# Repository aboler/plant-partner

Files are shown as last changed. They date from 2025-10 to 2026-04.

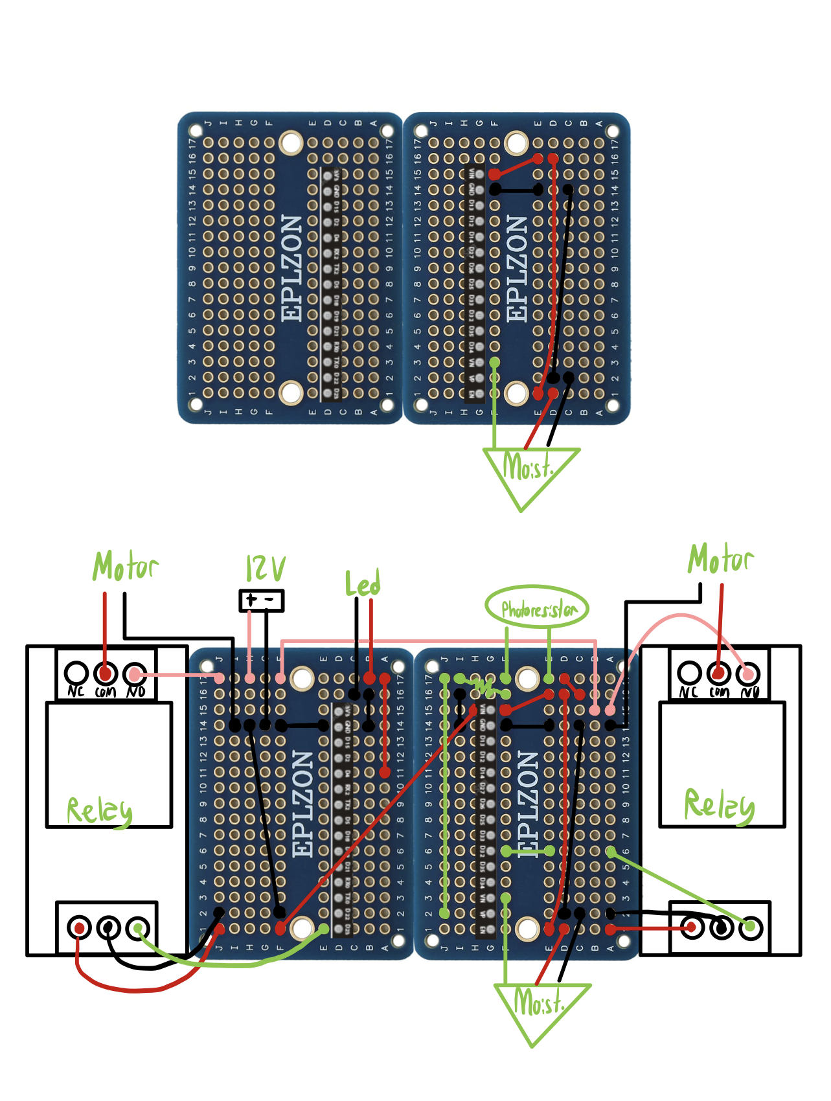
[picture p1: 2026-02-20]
Documentation/Diagrams/BetaBuild_Soldering_Moisture_TotalCircuit.png

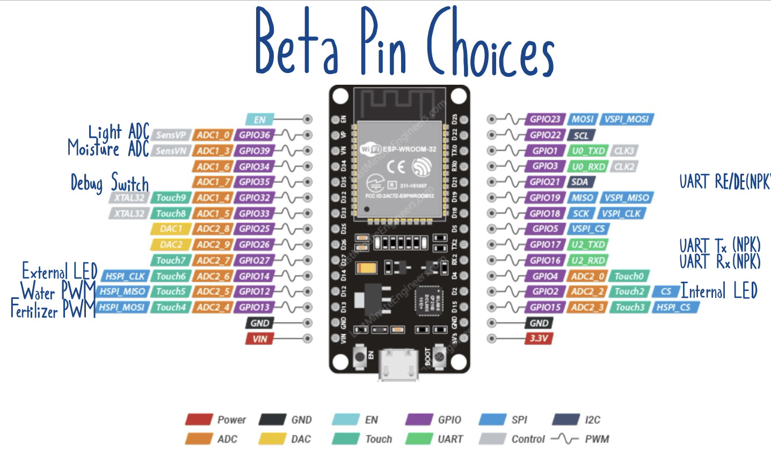
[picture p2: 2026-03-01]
Documentation/Diagrams/BetaBuild_Pinouts.png

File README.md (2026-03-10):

# plant-partner

Plant Partner repo. for CEN4908c

- **Contributors**: Nicholas Cimino, Aspen Boler, Sabrina Luu, Carter Kreis, Fernando Amado-Pupo
- [Project link](https://github.com/users/aboler/projects/1)

### Notes for adding code and time reports

- Please create a new branch to develop off of main
  - main remains as a minimum viable product branch available
  - Allows PR's to be made for adding to dev so group members can review code made
- Add reports for any changes/development work done in a day in main branch
  - Make reports in Documentation/Reports in relevant timesheet

## Meeting Times

- Meet weekly for ~15 minutes after every client meeting to ensure we're staying on track

## Completed Work

### Hardware Release

Please see ``Documentation/Diagrams``, ``Documentation/Circuits``, and ``Documentation/pcbDesign`` for current hardware designed, built, and used for testing

### Software Release

<ins>For ESP32 (in VSCode):</ins>

1. Run ``git clone recurse-submodules git@github.com:aboler/plant-partner.git``
   - This will clone the base plant-partner and esp-idf Github repositories using ssh
2. Download the ESP-IDF Extension
3. After you install the extension, the  should appear in the VS Code Activity bar (left side set of icons). When you click the Espressif icon, you can see a list of basic commands provided by this extension.
4. From the command list, select Configure ESP-IDF Extension or press F1 and type “Configure ESP-IDF Extension”. After, choose the ESP-IDF: Configure ESP-IDF Extension option.
5. Choose Express. Select Github for the download server.
6. For “Select ESP-IDF version” select “Find ESP-IDF in your system”
7. For “Enter ESP-IDF directory (IDF_PATH):” click the folder icon and within the Github Repository select /plant-partner/microSrc/submodules/esp-idf
8. For “Enter ESP-IDF Tools directory (IDF_TOOLS_PATH):” select the default location or wherever you prefer
   - Make sure that IDF_TOOLS_PATH had no spaces and is not in the Github Repo
9. If your operating system is MacOS/Linux, choose the system Python executable to create ESP-IDF virtual environment inside ESP-IDF Tools and install ESP-IDF Python package there
10. Click Install
11. If everything is installed correctly, you will see a message that all settings have been configured

In Powershell or a Linux terminal preferably:

1. Run ``cd microSrc``
2. Connect an ESP-32 into computer
3. Setup ESP-IDF and flash ESP-32 by running ``python esp.py -p PORT``
   - You may need to use python3 instead of python
   - PORT will be something like COM3 for Windows and /dev/ttyUSB0 for Ubuntu

<ins>For Backend + Database:</ins>

1. Navigate to ``backEndSrc/``
2. Start up the backend server by running ``npm start``, server will be running once these messages are displayed on the terminal
   - "Connected to MongoDB"
   - "Server running on port 8000"

<ins>For Frontend Application:</ins>

In Bash or Powershell

1. Run `cd frontEndSrc`
2. Run `cd frontend`
3. Run `flutter emulators –launch Medium_Phone_API_36.1`
4. Run `flutter pub get`
   * This command is to pull the dependencies
5. Run `flutter run`

### Pre-Alpha Build

- Ability to control GPIO Pins w/ ESP32.
  - i.e. controlling an external light source
  - Existing interfaces that allow modular control for project's purposes
- ADC data acquisition w/ ESP32
  - i.e. reading in value from photoresistor
  - Existing interfaces that allow modular control for project's purposes
- Developed basic structure to collect plant data from sensors
  - 3 uint16_t variables for collecting light, moisture, and nutrient data
- Breadboard implementation of our hardware/software
  - External photoresistor/LED circuit
- Frontend initial skeleton set up for mobile Android app interface
  - Configured Flutter environment and Android Emulator
  - Built a persistent bottom navigation bar (Tasks, Home, Settings)
  - Developed placeholder screens for each tab
  - Tested UI flow and verified emulator functionality
- Implemented locally-hosted database and backend API source code with basic functions
  - Set up MongoDB database that can be hosted locally, currently stores one JSON data model
  - Created Backend App source code with an API via Express.JS that allows for communication with the backend server and database
  - Organized the source code into folders for function controllers, JSON data models, and CRUD routes for easy addition of new functionality

### Prototype Build

- Ability to configure input GPIO Pins w/ ESP32
- Ability to generate a PWM signal
  - i.e. controlling a water pump omtor
- Modularized ADC data acquisition
  - Allows for configuration for both photoresistor and mositure sensor
- Modified breadboard implementation
  - Developed switch circuit to determine when to sample connected sensors/actuate components
  - e.g. water pump control, photoresistor and moisture sensing, LED actuation
- Ability to connect ESP32 to Wi-Fi
  - Allows new plant data to be sent to the database
- Created a test plant on the database
- Connected application and database so application can receive and display plant data to the Home tab
- Created a update button that allows application to display newly updated data from the database
- Beginnings of a PCB to replace external wiring has been started and posted to the repository
- Migrate database to the cloud via MongoDB atlas to allow for easier testing

### Alpha Build

- General clean up/organization in the code
- Modified ADC to be initialized through one function
- Modified main microcontroller loop to activate from one signal (currently a switch)
  - Reads all sensors
  - Activates actuators if needed
  - Sends data to database over Wi-Fi
- Created more permanent physical set up
  - Liquid tanks
  - Motor pumps in liquid tanks with elongated wires
  - Central cup to act as a pot
  - External carrying mechanism to more easily keep everything together
  - Smaller external circuit board
  - DAD program to act as switch, external LED, and proof that fertilizer motor activates when needed

### Beta Build

- Integrated MQTT messages to be sent from database/app. to initiate microcontroller main loop
  - ```plant_partner/act_tog_en```: toggle autocare enable
  - "plant_partner/ack"
    - w/ ```water``` msg.: actuate water pump, read moisture sensor, then report back data to the app.
    - w/ ```light``` msg.: toggle external LED, read photoresistor, then report back data to the app.
    - w/ ```nutrients``` msg.: actuate fertilizer pump
    - no message: read all of the sensors then report the data to the app.
      - If autocare enabled, then also actuate sensors based on if data requires it
- Finished and ordered PCB
- Soldered temporary physical board
- Instantiated and connected rough physical set up assembled in alpha build
- Added additional user features in the application:
  - Ability to toggle autocare and sync it with the microcontroller
  - button for actuating specific actuators
- Developed MQTT message functionality in the database
  - Time-based sample commands
  - Ability for specific actuation 

## Project Architecture

The ESP32 board is set up to interface with sensors to collect real-time environmental and system data. Currently, the microcontroller waits until it receives particular messages through an MQTT client. Depending on the message it can do the following: 1) toggle if autocare is enabled or disabled, 2) samples sensors, communicate data to the app., and actuate (if autocare on), 3) actuate a specific actuator (i.e. LED, water pump, fertilizer pump). These messages are currently being sent from the application while the sensor data is being communicated to the database.

The sensor readings can be reported to the database and displayed on a mobile application, providing users with remote monitoring. To update the data shown on the application, users must press the update button available in the Home tab. Additionally, there's a scheduling tab available where the autocare feature can be toggled as well as three actuator specific buttons for directly affecting specific devices.

### File Structure Summary

- ``microsrc`` : directory containing relevant ESP32 code
  - ``scripts`` : directory containing scripts necessary for setting up ESP-IDF dependencies and environment for device
  - ``src`` : directory containing all developed code for the program and a CMakeLists.txt to help compile
    - ``main`` : contains main program for ESP32 and CMakeLists.txt compiling developed code
    - ``dataTypes`` : contains code defining common data types created for the project, like plantData
    - ``peripherals`` : code for modularizing intercations with certain peripheral systems, like ADC, GPIO, and PWM
    - ``wifi`` : code for implementing wifi communication in the esp32
  - ``submodules`` : directory containing other repositories utilized within the main code
    - ``esp-idf`` : submodule containing examples and ESP32 interfaces in c
  - ``esp.py`` : Python script which can setup, build, flash, and/or monitor ESP-32
- ``backEndSrc`` : directory containing relevant backend code

  - ``controller`` : directory containing code for controllers that implement backend API CRUD functions for the server
    - ``sensorController.js`` : code for implementing CRUD functions that work with JSON data of the Sensor model
  - ``model`` : directory containing code for JSON data models to be used by the backend server and MongoDB database
    - ``sensorModel.js`` : code for creating the JSON Sensor data model
  - ``routes`` : directory containing code for the API's routes that allow CRUD functions to be accessed via URI in an HTTP request
    - ``sensorRoute.js`` : code for the routes that make use of functions that work with the Sensor JSON data model
  - ``node_modules`` : directory containing the node.js dependencies needed to create the backend code
  - ``.env`` : file that holds environment variables to be used by the main code of the backend server, app.js
  - ``app.js`` : the main code of the backend server, connecting to the mongoDB database, linking the routes, and locally hosting server
  - ``package-lock.json`` : the package-lock file for all the node package dependencies needed for the backend server
  - ``package.json`` : the package file listing the basic details and dependencies of the backend server project
- ``frontEndSrc`` : directory containing all Flutter/Dart source code for the mobile application.

  - ``lib``: root directory for all application logic, user interface screens, and services.
    - ``main``: application entry point; initializes the app and launches the bottom navigation shell
    - `nav.dart/dashboard_nav.dart`: bottom navigation bar widget and screen routing logic
    - ``views/``: directory containing all primary UI pages
      - `homeView.dart`: displays live plant sensor data from MongoDB and includes refresh functionality.
      - `taskView.dart/settingsView.dart:` placeholder screen for task/scheduling and user settings
      - `addPlantView.dart`: screen for adding new plants (prototype stage)
    - `services/`: directory for backend communication modules
      - `remote_service.dart`: handles HTTP requests to the backend
    - `plant.dart`: types data model used to decode JSON plant objects from the database

- ``Documentation`` : directory containing relevant project documentation
  - ``Circuits`` : directory containing relevant circuits created during development
  - ``ClassSubmissions`` : directory containing a file with the link to the Google Drive folder containing all of our report work/submissions
  - ``Contributions`` : directory containing all members' timesheet records
  - ``Datasheets`` : directory containing schematics to reference for our current materials being used
  - ``Diagrams`` : directory containing relevant diagrams created during development
  - ``Materials`` : directory containing documentation related to materials, such as which items were purchased and from where
  - ``Mosquitto`` : directory containing configuration files needed to successfully run mosquitto with our program
  - ``Research`` : directory containing research collected during the project, such as how to set up a coding environment for the ESP32
  - ``pcbDesign`` : directory containing work dones towards designing/building our project's PCB

## How to Use esp.py

PORT: This is USB port that the ESP-32 is connected to. For Windows, it should be COM3 or something similar. For Ubuntu, it should be ``/dev/ttyUSB0`` or something similar. Be aware, that if the Port is not automatically detected (usually Windows) you may have to install a driver being Silicon Labs CP210x or FTDI.

- Default: ``python esp.py -p PORT``
  - This will run the necessary setup scripts to install the ESP-IDF dependencies then build, flash, and monitor the ESP-32 at PORT
- Build: ``python esp.py build``
  - This will only build the current code under microSrc/src
- Flash: ``python esp.py flash -p PORT``
  - This will build and flash the current code under microSrc/src onto the ESP-32 at the connected Port
- Monitor: ``python esp.py monitor -p PORT``
  - This will monitor the ESP-32 at the connected Port and fill the terminal with any outputs from the ESP-32
- Clean: ``python esp.py clean``
  - This will delete any build artifacts

N.B. You may have to use python3 instead of python

## Current Bugs:

The system is in a development state with only base-level functionality implemented. No bugs reported

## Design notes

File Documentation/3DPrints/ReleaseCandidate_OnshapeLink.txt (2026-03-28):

Release Candidate:
https://cad.onshape.com/documents/16ddb73816ba2f326a677512/w/f05236e3a09f18a2d03a4be6/e/e1413465b117eccbdb8666b1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

Release Candidate Fix:
https://cad.onshape.com/documents/8866bfa4c7f7b88170b70fe7/w/29c6b3a1f68dc6e10564c710/e/2286aab6ed8d3c84d318de95

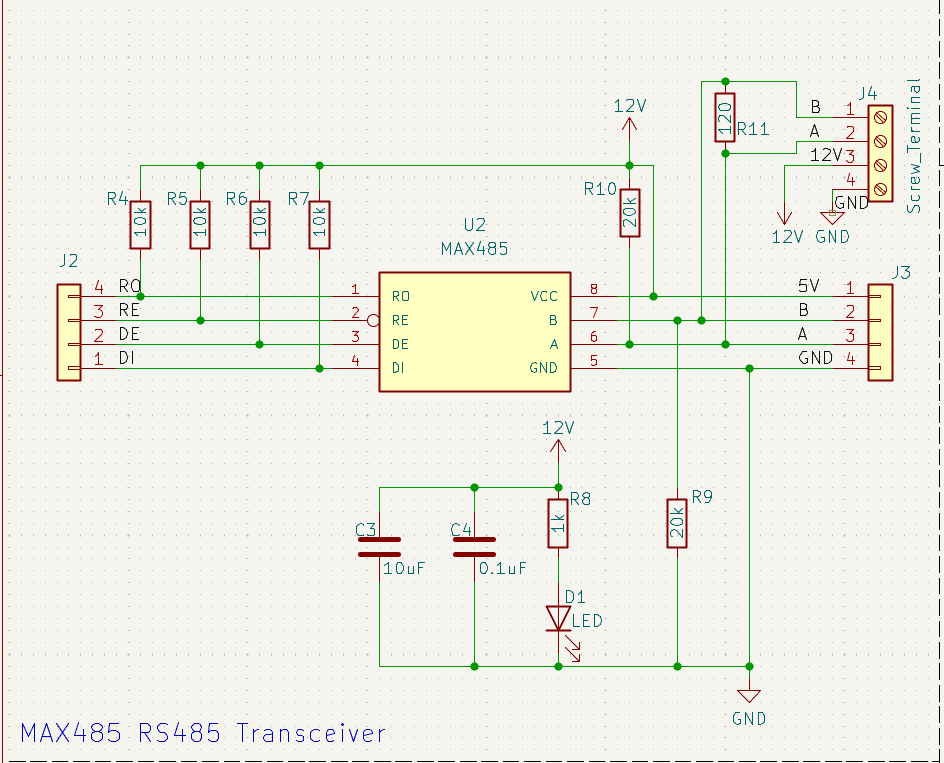
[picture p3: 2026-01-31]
Documentation/Diagrams/PCB_RS485Schematic.png

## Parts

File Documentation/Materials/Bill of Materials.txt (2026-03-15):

CEN4907C 
Plant-Partner 
Bill of Materials Draft

______________________________________
uController: ESP32Wroom: https://www.alibaba.com/product-detail/esp32-dev-kit-c-devkitc-v4_1600232911068.html
https://www.amazon.com/ESP-WROOM-32-Development-Microcontroller-Integrated-Compatible/dp/B08D5ZD528?th=1
______________________________________
Sensors:
NPK:
https://www.alibaba.com/product-detail/7-in-1-Soil-Integrated-Sensor_1601229125395.html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
Communication Protocol: Outputs RS485

Corossion Resistance Capacitive Soil Moisture Sensor:
https://www.amazon.com/Gikfun-Capacitive-Corrosion-Resistant-Detection/dp/B07H3P1NRM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
Communication Protocol: Analog to Digital (5V input voltage with output voltage of 0-3V)
Documentation links: https://www.circuitschools.com/interface-capacitive-soil-moisture-sensor-v1-2-with-arduino-lcd-and-oled/ & https://forum.arduino.cc/t/making-sense-of-moisture-sensor-readings/1382304/17
Notes: Uses JST-PH connector (the one with clasps) and a Dupont connector (the shielded one that just slides in)

Photoresistor (Ambient Light Sensor):
https://www.amazon.com/BOJACK-Photoresistance-Sensitive-Resistor-GM5539/dp/B08BKRPBVL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
Communication Protocol: Analog to Digital
Documentation links: https://www.micros.com.pl/mediaserver/info-orrgl5539.pdf 

RS485-UART Transceiver:
https://www.amazon.com/Transceiver-Featuring-Instrument-Communication-Development/dp/B00NIOLNAG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
Communication Protocol: Takes in RS485 from NPK Sensor and turns it to UART
Documentation Links: https://www.flywing-tech.com/blog/max485-ic-rs-485-communication-driver-pinout-datasheet-applications/ 

______________________________________
Pump Circuit:
* Makerverse Motor Controller: 
https://core-electronics.com.au/makerverse-motor-driver-2-channel.html
Communication Protocol: PWM 

Fluid Motor Pumps:
https://www.amazon.com/ALAMSCN-Submersible-Aquariums-Fountain-Hydroponics/dp/B08PBQ1N1G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
Thread Size: 12/24

5V Relay:
https://www.amazon.com/AEDIKO-Channel-Optocoupler-Isolation-Support/dp/B095YD3732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
Documentation: https://k6jca.blogspot.com/2022/05/schematic-amazon-relay-module-1-channel.html
 ______________________________________
Power Supply
12 V adapter:
https://www.alibaba.com/product-detail/Factory-Price-OEM-FCC-RoHS-Power_1600555965961.html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

Buck Converter down to 	5 V:
https://www.adafruit.com/product/4739
Documentation: Schematic file is in Documentation/Datasheets and the KiCad Project for it is in pcbDesign/buckConverter

LED Lamp 5V:
https://www.amazon.com/dp/B084ZNG43H?ref=ppx_yo2ov_dt_b_fed_asin_title
______________________________________
Container:
Lamp arm:
https://www.amazon.com/dp/B01HTIQD5G?ref=ppx_yo2ov_dt_b_fed_asin_title&th=1

Water/Fertilizer containers:
https://www.amazon.com/dp/B0DZNPPJRY?ref=ppx_yo2ov_dt_b_fed_asin_title

Resources:
Sensors:
NPK: https://www.instructables.com/Arduino-Soil-NPK-Sensor-Maximizing-Plant-Nutrition/
Pump:
https://core-electronics.com.au/guides/arduino/how-to-control-a-pump-with-an-arduino/

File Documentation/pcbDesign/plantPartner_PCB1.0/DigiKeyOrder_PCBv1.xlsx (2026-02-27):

# | QUANTITY | PART NUMBER | MANUFACTURER PART NUMBER | DESCRIPTION | CUSTOMER REFERENCE | BACKORDER | UNIT PRICE | EXTENDED PRICE
1 | 12 | 2057-PH2-08-UA-ND | PH2-08-UA | CONN HEADER VERT 8POS 2.54MM |  | 0 | 0.128 | 1.54
2 | 10 | 732-5327-ND | 61301611121 | CONN HEADER VERT 16POS 2.54MM |  | 0 | 0.752 | 7.52
3 | 10 | 1080-1037-ND | EL357N-G | OPTOISO 3.75KV 1CH TRANS 4-SOP |  | 0 | 0.394 | 3.94
4 | 4 | CP-002A-ND | PJ-002A | CONN PWR JACK 2X5.5MM SOLDER |  | 0 | 0.47 | 1.88
5 | 6 | ED10561-ND | OSTVN02A150 | TERM BLK 2P SIDE ENT 2.54MM PCB |  | 0 | 0.87 | 5.22
6 | 6 | ED10562-ND | OSTVN03A150 | TERM BLK 3P SIDE ENT 2.54MM PCB |  | 0 | 1.26 | 7.56
7 | 3 | ED10563-ND | OSTVN04A150 | TERM BLK 4P SIDE ENT 2.54MM PCB |  | 0 | 1.63 | 4.89

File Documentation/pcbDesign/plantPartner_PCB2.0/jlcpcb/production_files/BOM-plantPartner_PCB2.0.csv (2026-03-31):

Comment | Designator | Footprint | LCSC | Quantity
0.1uF | C7,C8 | C_0603_1608Metric | C14663 | 2
0.1uF | C4 | C_0402_1005Metric | C1525 | 1
100 | R13,R15,R25 | R_0402_1005Metric | C25076 | 3
100k | R1,R2 | R_0402_1005Metric | C25741 | 2
10k | R14,R16,R27,R4,R5,R6,R7 | R_0402_1005Metric | C25744 | 7
10uF | C3 | C_0402_1005Metric | C15525 | 1
120 | R11 | R_0402_1005Metric | C25079 | 1
18k | R3 | R_0603_1608Metric | C25810 | 1
1k | R12,R22,R23,R24,R8 | R_0402_1005Metric | C11702 | 5
20k | R10,R9 | R_0402_1005Metric | C25765 | 2
22uF | C1,C2 | C_0603_1608Metric | C59461 | 2
47uF | C10,C5,C6,C9 | C_0805_2012Metric | C16780 | 4
680 | R17 | R_0603_1608Metric | C23228 | 1
AO3400A | Q1,Q2,Q4 | SOT-23 | C20917 | 3
LED | D1,D10,D4 | LED_0603_1608Metric | C2286 | 3
MAX485 | U2 | SO08 | C19738 | 1
MPM3610 | IC1 | MPM3610 | C5173872 | 1
SS14 | D2,D3,D5,D6 | D_SMA | C2480 | 4
ESP32-DEVKIT-V1 | U3 | MODULE_ESP32_DEVKIT_V1 |  | 1
Screw_Terminal_01x02 | J30 | TerminalBlock_Phoenix_MPT-0,5-2-2.54_1x02_P2.54mm_Horizontal |  | 1
Conn_01x02 | J29 | PinHeader_1x02_P2.54mm_Vertical |  | 1
Conn_01x01 | J28 | PinHeader_1x01_P2.54mm_Vertical |  | 1
Conn_01x01 | J27 | PinHeader_1x01_P2.54mm_Vertical |  | 1
Conn_01x01 | J26 | PinHeader_1x01_P2.54mm_Vertical |  | 1
Conn_01x01 | J25 | PinHeader_1x01_P2.54mm_Vertical |  | 1
Conn_01x01 | J23 | PinHeader_1x01_P2.54mm_Vertical |  | 1
Conn_01x04 | J22 | PinHeader_1x04_P2.54mm_Vertical |  | 1
Conn_01x05 | J21 | PinHeader_1x05_P2.54mm_Vertical |  | 1
Conn_01x04 | J20 | PinHeader_1x04_P2.54mm_Vertical |  | 1
Conn_01x03 | J17 | PinHeader_1x03_P2.54mm_Vertical |  | 1
Conn_01x01 | J16 | PinHeader_1x01_P2.54mm_Vertical |  | 1
Conn_01x02 | J11 | PinHeader_1x02_P2.54mm_Vertical |  | 1
Screw_Terminal_01x02 | J10 | TerminalBlock_Phoenix_MPT-0,5-2-2.54_1x02_P2.54mm_Horizontal |  | 1
Screw_Terminal_01x02 | J9 | TerminalBlock_Phoenix_MPT-0,5-2-2.54_1x02_P2.54mm_Horizontal |  | 1
Conn_01x01 | J8 | PinHeader_1x01_P2.54mm_Vertical |  | 1
Screw_Terminal_01x02 | J7 | TerminalBlock_Phoenix_MPT-0,5-2-2.54_1x02_P2.54mm_Horizontal |  | 1
Barrel_Jack | J6 | BarrelJack_GCT_DCJ200-10-A_Horizontal |  | 1
Conn_01x02 | J5 | PinHeader_1x02_P2.54mm_Vertical |  | 1
Screw_Terminal_01x04 | J4 | TerminalBlock_Phoenix_MPT-0,5-4-2.54_1x04_P2.54mm_Horizontal |  | 1
Conn_01x04 | J3 | PinHeader_1x04_P2.54mm_Vertical |  | 1
Conn_01x04 | J2 | PinHeader_1x04_P2.54mm_Vertical |  | 1
Conn_01x04 | J1 | PinHeader_1x04_P2.54mm_Vertical |  | 1
Conn_01x03 | J13 | PinHeader_1x03_P2.54mm_Vertical |  | 1
Conn_01x03 | J12 | PinHeader_1x03_P2.54mm_Vertical |  | 1
Conn_01x03 | J14 | PinHeader_1x03_P2.54mm_Vertical |  | 1
Conn_01x03 | J18 | PinHeader_1x03_P2.54mm_Vertical |  | 1
Conn_01x03 | J15 | PinHeader_1x03_P2.54mm_Vertical |  | 1
Conn_01x04 | J19 | PinHeader_1x04_P2.54mm_Vertical |  | 1

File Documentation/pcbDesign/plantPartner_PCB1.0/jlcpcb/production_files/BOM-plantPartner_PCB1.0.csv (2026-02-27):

Comment | Designator | Footprint | LCSC | Quantity
0.1uF | C4 | C_0402_1005Metric | C1525 | 1
100 | R25 | R_0402_1005Metric | C25076 | 1
100k | R1,R2 | R_0402_1005Metric | C25741 | 2
10k | R14,R19,R27,R4,R5,R6,R7 | R_0402_1005Metric | C25744 | 7
10uF | C3 | C_0402_1005Metric | C15525 | 1
120 | R11 | R_0402_1005Metric | C25079 | 1
1N4148W | D4,D7 | D_SOD-123 | C2128 | 2
1k | R12,R16,R17,R21,R22,R23,R24,R26,R8 | R_0402_1005Metric | C11702 | 9
20k | R10,R9 | R_0402_1005Metric | C25765 | 2
22uF | C1,C2 | C_0603_1608Metric | C59461 | 2
470 | R15,R20 | R_0402_1005Metric | C25117 | 2
AO3400A | Q4 | SOT-23 | C20917 | 1
LED | D1,D10,D11,D2,D3,D5,D6 | LED_0603_1608Metric | C2286 | 7
PNP | Q1,Q2 | TO-92 | C8326 | 2
SS14 | D8,D9 | D_SMA | C2480 | 2
Conn_02x04_Top_Bottom | J20 | PinHeader_2x04_P2.54mm_Vertical |  | 1
500 | R13 | R_0603_1608Metric |  | 1
Screw_Terminal_01x02 | J30 | TerminalBlock_Phoenix_MPT-0,5-2-2.54_1x02_P2.54mm_Horizontal |  | 1
Conn_01x04 | J1 | PinHeader_1x04_P2.54mm_Vertical |  | 1
Screw_Terminal | J4 | TerminalBlock_Phoenix_MPT-0,5-4-2.54_1x04_P2.54mm_Horizontal |  | 1
Conn_01x04 | J16 | PinHeader_1x04_P2.54mm_Vertical |  | 1
Conn_01x02 | J11 | PinHeader_1x02_P2.54mm_Vertical |  | 1
Conn_02x04_Top_Bottom | J8 | PinHeader_2x04_P2.54mm_Vertical |  | 1
Conn_01x01 | J27 | PinHeader_1x01_P2.54mm_Vertical |  | 1
Conn_01x04 | J22 | PinHeader_1x04_P2.54mm_Vertical |  | 1
Conn_01x02 | J29 | PinHeader_1x02_P2.54mm_Vertical |  | 1
MAX485 | U2 | SO08 |  | 1
Conn_01x04 | J3 | PinHeader_1x04_P2.54mm_Vertical |  | 1
Conn_01x01 | J26 | PinHeader_1x01_P2.54mm_Vertical |  | 1
SRD-05VDC-SL-C | K2 | RELAY_SRD-05VDC-SL-C |  | 1
Conn_01x04 | J2 | PinHeader_1x04_P2.54mm_Vertical |  | 1
Conn_01x02 | J5 | PinHeader_1x02_P2.54mm_Vertical |  | 1
Conn_01x03 | J24 | PinHeader_1x03_P2.54mm_Vertical |  | 1
EL357N-G | U4 | OPTO_EL357N-G |  | 1
Conn_01x03 | J9 | PinHeader_1x03_P2.54mm_Vertical |  | 1
18.7k | R3 | R_0603_1608Metric |  | 1
Conn_01x03 | J25 | PinHeader_1x03_P2.54mm_Vertical |  | 1
500 | R18 | R_0603_1608Metric |  | 1
Conn_01x03 | J14 | PinHeader_1x03_P2.54mm_Vertical |  | 1
Conn_01x03 | J12 | PinHeader_1x03_P2.54mm_Vertical |  | 1
Conn_01x03 | J17 | PinHeader_1x03_P2.54mm_Vertical |  | 1
Conn_01x04 | J21 | PinHeader_1x04_P2.54mm_Vertical |  | 1
Screw_Terminal_01x03 | J6 | TerminalBlock_Phoenix_MPT-0,5-3-2.54_1x03_P2.54mm_Horizontal |  | 1
Conn_01x03 | J7 | PinHeader_1x03_P2.54mm_Vertical |  | 1
MPM3610 | IC1 | MPM3610 |  | 1
Screw_Terminal_01x02 | J18 | TerminalBlock_Phoenix_MPT-0,5-2-2.54_1x02_P2.54mm_Horizontal |  | 1
Conn_01x01 | J28 | PinHeader_1x01_P2.54mm_Vertical |  | 1
ESP32-DEVKIT-V1 | U3 | MODULE_ESP32_DEVKIT_V1 |  | 1
SRD-05VDC-SL-C | K1 | RELAY_SRD-05VDC-SL-C |  | 1
Conn_01x03 | J15 | PinHeader_1x03_P2.54mm_Vertical |  | 1
Conn_01x03 | J13 | PinHeader_1x03_P2.54mm_Vertical |  | 1
Conn_01x01 | J23 | PinHeader_1x01_P2.54mm_Vertical |  | 1
Screw_Terminal_01x03 | J10 | TerminalBlock_Phoenix_MPT-0,5-3-2.54_1x03_P2.54mm_Horizontal |  | 1
Barrel_Jack | J19 | BarrelJack_GCT_DCJ200-10-A_Horizontal |  | 1
EL357N-G | U1 | OPTO_EL357N-G |  | 1

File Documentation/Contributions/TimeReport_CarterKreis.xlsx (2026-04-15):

Name: | Carter Kreis |  | Total Time: | 155:03:00
Date: | General Category: | Starting Time: | Ending Time: | Calculated Time Worked: | Description:
2025-10-03 | Design Draft | 11:17:00 | 14:39:00 | 3:22:00 | Sat down with group after class to define project and talk through all of Design Draft points (Deliverables, Requirements, Division of work, ect.)
2025-10-06 | Check-in | 15:00:00 | 15:32:00 | 0:32:00 | Check-in 1: Met with group & Tyler. Discussed our design draft, and asked questions regarding design plan and material buying
2025-10-12 | Project Organization | 19:17:00 | 20:00:00 | 0:43:00 | Researched and implemented Github webhook which sends all updates from Github to Discord channel named github-updates
2025-10-14 | Check-in | 11:20:00 | 11:51:00 | 0:31:00 | Check-in 2: Met with group & Tyler. Reviewed out submitted design draft, discussed adding more hardware specification, and discussed with group members to start buying materials and beginning research
2025-10-20 | Check-in | 15:00:00 | 15:32:00 | 0:32:00 | Check-in 3: Met with group & Tyler. Planned out pre-alpha build documentation, materials list, and basic codebase structure. I will be working on PCB Design and physical materials for prototypes
2025-10-20 | Pre-Alpha Build | 21:45:00 | 22:15:00 | 0:30:00 | Researched and begun setup of ESP-IDF through its VS Code extension
2025-10-24 | Pre-Alpha Build | 14:30:00 | 16:05:00 | 1:35:00 | Setup ESP-IDF extension in VS Code. Attempted Hello World example code but my laptop is not detecting ESP32 as a COM Port. We also continued to plan Pre-Alpha Build goal
2025-10-24 | Pre-Alpha Build | 19:15:00 | 20:58:00 | 1:43:00 | Repeated issues with recursively cloning the submodule esp-idf. Cloning into the submodule itself took 10-12 minutes and the first two times some of the directories failed to clone on time.
2025-10-25 | Pre-Alpha Build | 10:05:00 | 17:42:00 | 7:37:00 | Finally got the ESP-IDF to flash ESP32 after switching to my Ubuntu OS. Proceeded to research and write the code to turn on external GPIO LED that is wired on breadboard and on-board LED. Also helped containerize, clean-up, and comment overall code for Pre-Alpha Build
2025-11-04 | Design Prototype | 9:05:00 | 11:05:00 | 2:00:00 | Worked on trying to get the specific ESP-32 model by analyzing the ESP32 info structs. I also got ESP-IDF working on Windows which needed some drivers uninstalled then proper ones re-installed
2025-11-04 | Design Prototype | 13:45:00 | 14:35:00 | 0:50:00 | Setup KiCad for PCB Design. Throughout this week and the next, I will figure out specific footprints for out sensors and design the PCB Schematic and then PCB design
2025-11-06 | Design Prototype | 10:05:00 | 13:57:00 | 3:52:00 | Searched for and found my Infinity Stones (the schematics for each sensor for our PCB). Now that I gathered the schematics, I can start designing the PCB layout and how it will fit into our overall project and Design Prototype
2025-11-10 | Design Prototype | 13:30:00 | 15:51:00 | 2:21:00 | Finished PCB Schematic for Buck Converter and now working on RS-485 Transceiver Schematic.
2025-11-11 | Design Prototype | 10:30:00 | 13:00:00 | 2:30:00 | Worked on UART driver code which includes an init, read, and write functions for standard UART modules and also a skeleton for RS-485 Half-duplex UART communication with the same three main functions (init, read, write)
2025-11-13 | Design Prototype | 11:10:00 | 17:30:00 | 6:20:00 | Finished up UART driver to have init, read, and write functionality. I had to add a write_string and write_int function to make it more multi-purpose. Now its time to get the NPK Sensor readings from the RS-485 Transceiver (usins RS-485 UART mode doesn't seem practical now)
2025-11-14 | Design Prototype | 17:00:00 | 21:45:00 | 4:45:00 | With the UART driver finished, I moved onto adjusting those functions to fit NPK Sensor → RS485 Transceiver → ESP-32 Communication. With the help of Rob and some sketchy datasheets (our NPK Sensor did not provide one), I was able to receive data from the NPK Sensor. With the lack of a datasheet, we will have to test which registers contain what values, but we are at least receiving data from the sensor.
2025-11-15 | Design Prototype | 9:30:00 | 10:15:00 | 0:45:00 | Wrote initial code for espRun.sh script which should source, build, flash and monitor ESP-32 with one command. I will come back to finish and test this
2025-11-15 | Design Prototype | 14:15:00 | 20:30:00 | 6:15:00 | Finished up scripts to make working with esp-32 easier. I decided to have an intial setup script for each OS and then a big python script for actually running the configured setup. This should make development a lot more straightforward
2025-11-16 | Design Prototype | 17:15:00 | 19:15:00 | 2:00:00 | Finalized scripts for Windows since Windows is more sensitive. I ran into an issue where I wasn't calling export.bat where needed to setup idf.py but I added that call and now the script works with windows as well :)
2025-11-17 | Design Prototype | 13:05:00 | 15:35:00 | 2:30:00 | I finished the RS485 Transceiver Schematic. Added ESP32 Symbol to PCB Schematic and begun implementing 12V Relay circuit which is not looking fun
2026-01-02 | Alpha Build | 11:40:00 | 16:15:00 | 4:35:00 | After completing the 12V relay Schematic with a custom made Symbol and imported footprints, I realized that we are using 5V relays. So I have to spend more time recalculating for 5V relay values as the only schematic I could find was for the 12V.
2026-01-05 | Alpha Build | 12:15:00 | 13:45:00 | 1:30:00 | I figured out the values for the 5V relay Schematic. Next I’ll need to verify the values and then add our 12V AC/DC input to finish the schematic. Then comes laying out the PCB
2026-01-06 | Alpha Build | 9:45:00 | 11:30:00 | 1:45:00 | Added in the rest of my 5V relay Schematic component values since I got interrupted yesterday. I also found the footprints for main components in the circuit.
2026-01-23 | Alpha Build | 10:45:00 | 13:55:00 | 3:10:00 | Verified the Schematics for the RS-485 Transceiver and Buck Converter. I will verify the 5V Relay next add the 12V AC/DC input and then start routing the PCB itself (need to get here ASAP)
2026-01-24 | Alpha Build | 15:15:00 | 17:45:00 | 2:30:00 | Started verification on the 5V Relay and overestimated my circuit simulation knowledge. I started with KiCad which was bad then moved to Ltspice all while trying to simulate 5V Relay functionality with SPICE components
2026-01-26 | Alpha Build | 12:10:00 | 16:55:00 | 4:45:00 | Verified the 5V Relay in Ltspice. Now cross-checking that all the symbols and footprints match up. I also gathered some 3D models that I was missing for some components. Next, I will verify the optocoupler symbol and footprint (I think I found a better one) and then add pins to debug the PCB once printed.
2026-01-28 | Alpha Build | 16:25:00 | 18:35:00 | 2:10:00 | Put in the correct ESP32 (DEVKIT-V1) into Schematic. Updated the IO pin connections for ESP. Added Power supply system to SChematic. Need to update optocoupler symbol and footprint. Then routing shall commence
2026-01-29 | Alpha Build & Prof. Meeting | 10:10:00 | 13:10:00 | 3:00:00 | Added the small circuitry needed for ADC sensors, ESP-32 External LED, Overall PCB Heartbeat sensor. Fixed wiring issue with 5V Relays. Met with Prof. Alex about our Alpha Build status. I tried to add new optocoupler symbol and footprint but KiCad could not find it for some reason (rip). Now I need to add used ESP-32 pins, extra 5V and 12V pins, extra GND pins, and unused ESP32 Pins, THEN finally I can route (I hope … please lol).
2026-01-30 | Alpha Build | 22:00:00 | 23:15:00 | 1:15:00 | Added the optocoupler, additional 5V, 12V, and GND testing pins. Added footprints to any symbols that were missing them. Begun labeling unused ESP32 Pins on Schematic. Will add testing pins for used and unused ESP32 Pins next then routing (finally)
2026-02-05 | Beta Build | 10:40:00 | 13:45:00 | 3:05:00 | Finished adding Testing Pins. Starting Routing by drawing it out and organizing components in PCB. Quickly realized that I incorrectly setup 5V and 12V labels so will need to re-label those soon
2026-02-06 | Beta Build & Alpha Demo | 10:30:00 | 12:20:00 | 1:50:00 | We showed off the Alpha Build to Tyler and I worked on the PCB Routing. I am trying to resolve the Electrical Rules Checker (ERC) now while routing.
2026-02-07 | Beta Build | 16:45:00 | 19:30:00 | 2:45:00 | Routed the 5V Relays and fixed a schematic issue I made with them. Next is the Buck Converter, RS485 Transceiver, Power Supplies, and ESP32 Signals
2026-02-09 | Beta Build | 15:00:00 | 16:55:00 | 1:55:00 | Finished RS485 Transceiver, working on Buck Converter and connecting signals. Need to Fix Buck Converter IC footprint
2026-02-10 | Beta Build | 10:40:00 | 12:30:00 | 1:50:00 | Fixed Buck Converter and routed it. Connected more majority of ESP signals and some of the debugging pins. Brought the size of PCB down to about 1/2 of the original. My goal is to finish by today and optimize size in the 2nd gen
2026-02-11 | Beta Build | 16:00:00 | 19:30:00 | 3:30:00 | Finished Routing (for now). I need to add silkscreens for debugging, then copper pour and probably other stuff. My goal is so have a JLCPCB order by tomorrow. I brought the PCB down to about the size of my phone
2026-02-12 | Beta Build | 12:15:00 | 14:00:00 | 1:45:00 | Meeting with Instructor for Beta Build. Will work on cleaning up the wires and lessening the space that our Beta Build Takes. Will work on 3D printed box to hide wires
2026-02-12 | Beta Build | 19:00:00 | 21:15:00 | 2:15:00 | Finished Labeling PCB (too much) and fixed DRC errors on PCB. Time to add copper pours, drill holes, and probably more, then review it with a TA, and make the order :)
2026-02-13 | Beta Build | 11:00:00 | 13:10:00 | 2:10:00 | Meeting with Tyler and then working on fully implementing the RS485 Transceiver into the overall project. I also started on the 5V Lamp circuit for the PCB now (I hate Ltspice)
2026-02-13 | Beta Build | 19:15:00 | 20:05:00 | 0:50:00 | Finally got LTspice sim to work and confirmed that Schematic is good. Time to implement into PCB
2026-02-14 | Beta Build | 18:00:00 | 19:30:00 | 1:30:00 | Added Lamp to PCB. Added Copper Pours and Drill Holes. Now fixing rude error about cap. not getting copper pour connection properly
2026-02-15 | Beta Build | 21:50:00 | 23:20:00 | 1:30:00 | Gerber and Drill files have been generated. I will order on JLCPCB tomorrow morning ASAP and then finish up cube for Beta
2026-02-17 | Beta Build | 10:35:00 | 12:45:00 | 2:10:00 | Made some adjustments to PCB to fit JLCPCB standards. When going to order PCB realized I needed LCSC values. I spent the rest of the time trying to setup the JLCPCB tools plugin with zero success.
2026-02-19 | Beta Build | 10:40:00 | 13:45:00 | 3:05:00 | I got the plugin finally working! I had some messed up Python modules that I had to remove and then reinstall. I have also now learned that the footprints I chose for the PCB were too small and classified as extended for JLCPCB which means more $$. So now I have to change all the Resistor, Capacitor, and Diode footprints to a bigger size to not cost too much. This will then also result in me having to route these small parts again. I am tired of my lack of PCB design knowledge but I think I might be done after this.
2026-02-19 | Beta Build | 15:55:00 | 18:15:00 | 2:20:00 | Rerouted the resistors, capacitors, and LEDs. Surely I can now generate the Drill & Gerber files for printing with no issues
2026-02-20 | Beta Build | 11:45:00 | 18:20:00 | 6:35:00 | I ordered the PCB!! … there is so many changes I want to make but I also just wanted to order it but without the revisions it was more expensive but now we at least will have a board. Welp, either way I will solve the NPK (again unfortunately) next and then after that get onto PCB V2 and then 3D modeling
2026-02-26 | Release Candidate | 11:55:00 | 14:20:00 | 2:25:00 | Researched more into implemented PWM driven MOSFET circuit to replace 5V relays. Tested liquid pumps to see what voltages were actually needed to power them and learned that 12V is wayyy overkill. I also finished schematic for new MOSFET circuits and will Ltspice next
2026-02-26 | Release Candidate | 18:20:00 | 19:50:00 | 1:30:00 | I still need to test MOSFET circuits in Ltspice but I cleaned up the v2 Schematic and starting routing v2 PCB
2026-02-28 | Release Candidate | 18:20:00 | 19:30:00 | 1:10:00 | Routed v2 PCB some more. Finished routing power sources, Buck Converter, MOSFET circuits, and most of RS485 Transceiver. I forgot about Ltspice but will not next time I get a big chunk of time
2026-03-02 | Release Candidate | 10:05:00 | 12:05:00 | 2:00:00 | Meeting with Tyler. Fully finished routing MOSFET circuits, RS485 Transceiver, and some of ADC circuits. Still need to test MOSFET circuits in Ltspice, but placed most of overall PCB into a small edge cut square that is 2.5”x2.5” which is 50% smaller and cheaper.
2026-03-02 | Release Candidate | 13:45:00 | 17:00:00 | 3:15:00 | Finished routing everything. Adding silkscreens and double checking details. Next I will test in Ltspice. Hopefully, place JLC order by tonight or tomorrow
2026-03-03 | Release Candidate | 11:30:00 | 14:15:00 | 2:45:00 | Ordered PCB v2 after verifying MOSFET PWM circuits in Ltspice!! It was definitely cheaper but still just over $50 for all 5 to be assembled with SMT parts. Next I’ll work on “solving” the NPK so we can implement it to the entire system.
2026-03-04 | Release Candidate | 13:55:00 | 17:55:00 | 4:00:00 | (1st Half) I made an oopsie with PCBv2 order so I had to fix that and in the meantime I found a cheaper solution that kept the same logic of the circuits. It saved us $10 yippee. (2nd Half) I got the NPK sensor working! I adjusted the CRC checker and added a delay when switching between Receive and Transmit mode. The data looks valid and increases or decreases when in or out of dirt. Next I'll clean up the uart_rs485_read function so you can just call it and get an array of the Nutrient values in their mg/kg form. I'll also see how many delays I can remove so this won't slow down the overall setup.
2026-03-10 | Release Candidate | 11:35:00 | 13:30:00 | 1:55:00 | Finalized 3D Modeling Design with Aspen and began soldering the testing pins for PCBv1
2026-03-12 | Release Candidate | 11:00:00 | 12:45:00 | 1:45:00 | Worked on soldering PCBv1 some more. Most of the testing pins are in and all the screw terminals are in. Next will be the two SMD parts and any of the more difficult parts.
2026-03-24 | Release Candidate | 12:35:00 | 15:30:00 | 2:55:00 | Worked on Documentation over break so that’s why the long gap, but today I helped finalize the 3D modeling for the Liquid Housing, PCB Housing, and PCB Lid by adding connector pins. I also spent some time helping Nico test the entire projects connectivity but we had issues connected to WiFi for HTTP communication.
2026-03-26 | Release Candidate | 12:15:00 | 14:30:00 | 2:15:00 | Added the connection holes for the Moisture Sensor and NPK but I can get part of the Moisture Sensor sketch to be fully defined
2026-03-27 | Release Candidate | 17:30:00 | 18:45:00 | 1:15:00 | Finished soldering the Final PCB from where Aspen left off. Then I powered it on and tested all the pins to verify that the power was properly being routed and not killing anything. The ESP and PCB are all powered!
2026-03-31 | Release Candidate | 11:25:00 | 16:30:00 | 5:05:00 | The PCB works!! We tested it with every sensor all at once and it worked beautifully. I helped figure out the connections for each sensor and device while also updating the pin assignments for the ESP code based on the PCB. I also added connector holes to the Lamp Handle for the 3D model
2026-04-02 | Release Candidate | 10:15:00 | 14:00:00 | 3:45:00 | Drilled holes for fertilizer and water pump tubes and power cords. Soldered wire extensions for Lamp then heat-shrinked and taped them. Attempted to desolder Light Sensor pins on PCB to swap for Female Headers but destroyed PCB pad. For Tyler Demo tomorrow, I will make some small external circuitry but I will help solder a new board by early next week.
2026-04-03 | Release Candidate | 10:15:00 | 11:35:00 | 1:20:00 | Since we burned the Light Sensor PCB Pad, I breadboarded a quick solution. Then we demo’d our project to Tyler who said everything was good.
2026-04-14 | Post-Mortem Presentation | 12:00:00 | 14:45:00 | 2:45:00 | Worked on redesigning our 3D print to not take as long which required reducing the thickness and moving some of the connection pins and holes
 |  |  |  | 0:00:00
 |  |  |  | 0:00:00
 |  |  |  | 0:00:00
 |  |  |  | 0:00:00
 |  |  |  | 0:00:00
 |  |  |  | 0:00:00
 |  |  |  | 0:00:00
 |  |  |  | 0:00:00
 |  |  |  | 0:00:00
 |  |  |  | 0:00:00
 |  |  |  | 0:00:00
 |  |  |  | 0:00:00
 |  |  |  | 0:00:00
 |  |  |  | 0:00:00
 |  |  |  | 0:00:00
 |  |  |  | 0:00:00
 |  |  |  | 0:00:00
 |  |  |  | 0:00:00
 |  |  |  | 0:00:00
 |  |  |  | 0:00:00
 |  |  |  | 0:00:00
 |  |  |  | 0:00:00
 |  |  |  | 0:00:00
 |  |  |  | 0:00:00
 |  |  |  | 0:00:00
 |  |  |  | 0:00:00
 |  |  |  | 0:00:00
 |  |  |  | 0:00:00
 |  |  |  | 0:00:00
 |  |  |  | 0:00:00
 |  |  |  | 0:00:00
 |  |  |  | 0:00:00
 |  |  |  | 0:00:00
 |  |  |  | 0:00:00
 |  |  |  | 0:00:00
 |  |  |  | 0:00:00
 |  |  |  | 0:00:00
 |  |  |  | 0:00:00
 |  |  |  | 0:00:00
 |  |  |  | 0:00:00
 |  |  |  | 0:00:00
 |  |  |  | 0:00:00
 |  |  |  | 0:00:00
 |  |  |  | 0:00:00
 |  |  |  | 0:00:00
 |  |  |  | 0:00:00
 |  |  |  | 0:00:00
 |  |  |  | 0:00:00
 |  |  |  | 0:00:00
 |  |  |  | 0:00:00
 |  |  |  | 0:00:00
 |  |  |  | 0:00:00
 |  |  |  | 0:00:00
 |  |  |  | 0:00:00
 |  |  |  | 0:00:00
 |  |  |  | 0:00:00
 |  |  |  | 0:00:00
 |  |  |  | 0:00:00
 |  |  |  | 0:00:00
 |  |  |  | 0:00:00
 |  |  |  | 0:00:00
 |  |  |  | 0:00:00
 |  |  |  | 0:00:00
 |  |  |  | 0:00:00
 |  |  |  | 0:00:00
 |  |  |  | 0:00:00
 |  |  |  | 0:00:00
 |  |  |  | 0:00:00
 |  |  |  | 0:00:00
 |  |  |  | 0:00:00
 |  |  |  | 0:00:00
 |  |  |  | 0:00:00
 |  |  |  | 0:00:00
 |  |  |  | 0:00:00
 |  |  |  | 0:00:00
 |  |  |  | 0:00:00
 |  |  |  | 0:00:00
 |  |  |  | 0:00:00
 |  |  |  | 0:00:00
 |  |  |  | 0:00:00
 |  |  |  | 0:00:00
 |  |  |  | 0:00:00
 |  |  |  | 0:00:00
 |  |  |  | 0:00:00
 |  |  |  | 0:00:00
 |  |  |  | 0:00:00
 |  |  |  | 0:00:00
 |  |  |  | 0:00:00
 |  |  |  | 0:00:00
 |  |  |  | 0:00:00
 |  |  |  | 0:00:00
 |  |  |  | 0:00:00
 |  |  |  | 0:00:00
 |  |  |  | 0:00:00
 |  |  |  | 0:00:00
 |  |  |  | 0:00:00
 |  |  |  | 0:00:00
 |  |  |  | 0:00:00
 |  |  |  | 0:00:00
 |  |  |  | 0:00:00
 |  |  |  | 0:00:00
 |  |  |  | 0:00:00
 |  |  |  | 0:00:00
 |  |  |  | 0:00:00
 |  |  |  | 0:00:00
 |  |  |  | 0:00:00
 |  |  |  | 0:00:00
 |  |  |  | 0:00:00
 |  |  |  | 0:00:00
 |  |  |  | 0:00:00
 |  |  |  | 0:00:00
 |  |  |  | 0:00:00
 |  |  |  | 0:00:00
 |  |  |  | 0:00:00
 |  |  |  | 0:00:00
 |  |  |  | 0:00:00
 |  |  |  | 0:00:00
 |  |  |  | 0:00:00
 |  |  |  | 0:00:00
 |  |  |  | 0:00:00
 |  |  |  | 0:00:00
 |  |  |  | 0:00:00
 |  |  |  | 0:00:00
 |  |  |  | 0:00:00
 |  |  |  | 0:00:00
 |  |  |  | 0:00:00
 |  |  |  | 0:00:00
 |  |  |  | 0:00:00
 |  |  |  | 0:00:00
 |  |  |  | 0:00:00
 |  |  |  | 0:00:00
 |  |  |  | 0:00:00
 |  |  |  | 0:00:00
 |  |  |  | 0:00:00
 |  |  |  | 0:00:00

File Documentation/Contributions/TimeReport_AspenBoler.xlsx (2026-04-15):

Name: | Aspen Boler |  | Total Time: | 176:14:00
Date: | General Category: | Starting Time: | Ending Time: | Calculated Time Worked: | Description:
2025-10-03 | Design Draft/Plans | 11:17:00 | 14:39:00 | 3:22:00 | Sat down with group after class to define project and talked through all of Design Draft points (Deliverables, Requirements, Division of work, ect.)
2025-10-04 | Design Draft | 10:17:00 | 11:55:00 | 1:38:00 | Researched and wrote description for the project's deliverable artifacts
2025-10-04 | Check-in | 17:05:00 | 17:35:00 | 0:30:00 | Reserved time slots for all of the group check-ins for Senior Design 1
2025-10-05 | Design Draft | 18:14:00 | 20:30:00 | 2:16:00 | Helped rework design draft to fit within word limit
2025-10-06 | Check-in | 15:00:00 | 15:32:00 | 0:32:00 | Check-in 1: Met with group & Tyler, discussed our design draft, and asked questions regarding design plan and material buying
2025-10-10 | GitHub Creation | 10:35:00 | 11:31:00 | 0:56:00 | Created repository, added members, created Project page, and created reports directory
2025-10-12 | Webhook Set-up | 20:15:00 | 20:31:00 | 0:16:00 | Helped Nicholas, according to research done by Carter Kreis, to set up and test Webhook so GitHub pushes would send to a discord channel
2025-10-14 | Check-in | 11:20:00 | 11:51:00 | 0:31:00 | Check-in 2: Met with group & Tyler, reviewed out submitted design draft, discussed adding more hardware specification, and discussed with group members to start buying materials and begin research
2025-10-17 | Timesheet | 15:00:00 | 16:00:00 | 1:00:00 | Created Timesheet template for all members
2025-10-20 | Check-in | 15:00:00 | 15:32:00 | 0:32:00 | Check-in 3: Met with group & Tyler, discussed things to prepare for alpha build completion and resources to buy
2025-10-24 | Research | 10:58:00 | 13:43:00 | 2:45:00 | Began researching ESP32-Wroom and how to develop code; Found IDF with example/interfaces and made into submodule; Used submodule to configure ESP_IDF on Vscode and examine example projects
2025-10-24 | Pre-Alpha Dev. | 14:30:00 | 21:17:00 | 6:47:00 | Flashed onto all three ESP32's, helped members install development on computers, defined structure for Sunday's end, created main skeleton, investigated examples to create hardware drivers
2025-10-25 | Pre-Alpha Dev. | 10:00:00 | 16:25:00 | 6:25:00 | Began writing report, determined how to integrate ADC into main alongside Fernando, began creating ADC peripheral interface and editted CMakeList.txt to include it after several attempts, tried to create ADC structure to center ADC initialization in one function but failed.
2025-10-25 | Pre-Alpha Dev. | 20:26:00 | 21:50:00 | 1:24:00 | Reviewed and editted cleaned up code/ReadMe, adjusted report
2025-10-26 | Pre-Alpha Dev. | 11:00:00 | 12:00:00 | 1:00:00 | Record and edit microprocessor portion of video
2025-10-26 | Pre-Alpha Dev. | 15:50:00 | 16:25:00 | 0:35:00 | Clean up readme and edit in frontend portion of video
2025-10-28 | Check-in | 11:20:00 | 11:50:00 | 0:30:00 | Check-in 4: Met with group & Tyler, discussed how we needed to begin implementing communication for the prototype. Sat down with group and designated work to reach these goals.
2025-11-04 | Check-in | 11:20:00 | 11:50:00 | 0:30:00 | Check-in 5: Met with group & Tyler, discussed work that was completed and set up group work day for following Thursday. Also discussed what work would be completed to meet goals and beginning communication and test sensors.
2025-11-06 | Prototype Dev. | 10:10:00 | 14:51:00 | 4:41:00 | Met with group to conduct work; Researched how to use 5V Micro Submersible Mini Water Pump, discovered it needed use of PWM, configured PWM in main to test it, developed PWM peripheral module to use in main, integrated it into main, added photos, created branch for another sensor
2025-11-09 | Prototype Dev. | 11:20:00 | 12:06:00 | 0:46:00 | Began researching how Capacitive Soil Moisture Sensor should interface with the microcontroller and the type of data it outputs, started deciding how to modify ADC code to generalize and be used for both photoresitor and this sensor, made modular way to declare ADC for light or moisture sensor
2025-11-09 | Prototype Dev. | 19:20:00 | 19:40:00 | 0:20:00 | Changed file name's of ADC and related dependencies to make the module more generalizable
2025-11-10 | Prototype Dev. | 15:00:00 | 15:30:00 | 0:30:00 | Check-in 6: Met with group & Tyler, updated everyone on features currently implemented and made plans for the following Tuesday for each person to complete
2025-11-11 | Prototype Dev. | 11:00:00 | 17:39:00 | 6:39:00 | Got together, started integrating ADC branch and rearranged main to work as desired for prototype, created GPIO for inputs and started investigating interrupt system, created external switch to interface with micro, looked into getting wifi created to flash onto ESP32
2025-11-13 | Prototype Dev. | 11:00:00 | 17:43:00 | 6:43:00 | Got together with group, started doing gpio integration to set up sensor set up, created prototype board, connected and tested moisture sensor, connected and tested new photoresistor, created wires for relay and power bank and tested water motor, editted main to reflect prototype behavior
2025-11-14 | Prototype Dev. | 11:45:00 | 13:30:00 | 1:45:00 | Began looking through project requirements and making adjustments to ensure issues were updated, naming conventions were followed
2025-11-14 | Prototype Dev. | 14:10:00 | 14:59:00 | 0:49:00 | Tested Fernando's Wi-Fi contributions, altered circuit, and uploaded finished circuit onto Github
2025-11-14 | Prototype Dev. | 15:00:00 | 18:14:00 | 3:14:00 | Continued documenting stuff for prototype submission, made circuit diagrams, editted some issues discussed what needed to be continued for submittables
2025-11-14 | Prototype Dev. | 21:34:00 | 22:56:00 | 1:22:00 | Modify project display, began creating report document
2025-11-15 | Prototype Dev. | 11:06:00 | 13:30:00 | 2:24:00 | Continuing report, modified readme
2025-11-15 | Prototype Dev. | 16:34:00 | 21:25:00 | 4:51:00 | Finished my portion of the report
2025-11-15 | Prototype Dev. | 21:38:00 | 22:05:00 | 0:27:00 | Modified ReadMe, modified plant structure
2025-11-16 | Prototype Dev. | 11:23:00 | 14:55:00 | 3:32:00 | Modified report and ReadMe, began working on presentation, assisted Fernando and Nicholas test the state of the Wi-Fi from an alternate computer and integrating it into main.
2025-11-16 | Prototype Dev. | 17:50:00 | 21:30:00 | 3:40:00 | Begin working on powerpoint
2026-01-08 | Alpha Build | 14:10:00 | 19:00:00 | 4:50:00 | Experimented with ADC peripheral on DAD and reworked the peripheral so it only needs to call an initialization function in main, reworked some aspects of main to avoid bad outputs/improve organization, removed extra plant data structure, created heartbeat module
2026-01-16 | Alpha Build | 16:08:00 | 17:59:00 | 1:51:00 | Changed personal directory name and it killed everything, took me an hour but it forced me to reinstall everything to get it working
2026-01-16 | Alpha Build | 17:59:00 | 19:57:00 | 1:58:00 | Started modifying main to more closely match a routine based off of received signal from database. Also made some tickets and cleaned up code to be more organized and efficient
2026-01-21 | Alpha Build | 13:05:00 | 14:06:00 | 1:01:00 | Created pin diagram showing which pins were used for what; Integrated fertilizer pump addition to PWM and main and tested it out
2026-01-23 | Check-in | 10:40:00 | 11:49:00 | 1:09:00 | Check-in 6: Met with group & Tyler, discussed what's gotten done and what needs to get done for alpha build, showed bought materials and began observing what modifications would be needed to integrate electronics into plastic build
2026-01-23 | Alpha Build | 17:30:00 | 18:31:00 | 1:01:00 | Realized I should go ahead and have main set up for potential of boolean to change depending on if auto-scheduling/care is on; Created/modified tickets in project hub.
2026-01-26 | Alpha Build | 14:00:00 | 17:03:00 | 3:03:00 | Integrated PR into main; solder and heat shrinked additional wires to extend motor wire length; Built new mini circuit to make cleaner and tested with new motors to ensure everything still worked.
2026-01-29 | Instructor Meeting | 10:55:00 | 11:35:00 | 0:40:00 | Met up with group and instructor to discuss current project state and what needs to be done for documentation; fixed wire that fell out
2026-01-29 | Alpha Build | 16:50:00 | 16:58:00 | 0:08:00 | Merged wire motor branch
2026-02-05 | Alpha Build | 10:40:00 | 14:00:00 | 3:20:00 | Met up with group to test demo. Also received another 12v to 5v adapt, so began wire stripping and attaching fertilizer motor to a new relay; Utilized double-sided tape to rework our wire structure to make it more sound/easier to use and understand
2026-02-06 | Check-in | 10:40:00 | 12:19:00 | 1:39:00 | Check-in 7: Met with group & Tyler to demo alpha build; Discussed what needed to be done and experimented with group to get MQTT client to send a signal to the microcontroller.
2026-02-10 | Beta Build | 10:40:00 | 14:00:00 | 3:20:00 | Experimented with group and successfully got MQTT client to communicate t microcontroller. Started modifying main so the main loop would be triggered from MQTT message
2026-02-10 | Beta Build | 19:41:00 | 20:47:00 | 1:06:00 | Began cleaning up MQTT branch to prepare it for more clean merge
2026-02-10 | Beta Build | 22:48:00 | 23:59:00 | 1:11:00 | Additional cleaning, fixed merge conficts, adjusted tickets. Tested to still be able to build/flash.
2026-02-11 | Beta Build | 0:00:00 | 0:21:00 | 0:21:00 | ^^ Had to split into 2 because excel hates new days.
2026-02-11 | Beta Build | 11:21:00 | 13:42:00 | 2:21:00 | Tested MQTT on my own computer to see it still works, merged into main, updated tickets, set up rest of the code needed to test NPK sensor in person
2026-02-11 | Beta Build | 18:30:00 | 19:49:00 | 1:19:00 | Tried to flash uart to see what would happen if test ran without sensor connected and realized current pin set up killed the micro.; switched pins until main worked again, now ready for test tomorrow in person
2026-02-12 | Beta Build | 10:50:00 | 12:20:00 | 1:30:00 | Began attempting to connect NPK to microcontroller to test uart
2026-02-12 | Instructor Meeting | 12:20:00 | 12:49:00 | 0:29:00 | Met up with group and instructor to discuss current project state and what needs to be done for documentation;
2026-02-13 | Beta Build | 12:49:00 | 14:24:00 | 1:35:00 | Discussed with group our plans to get everything completed before beta uild. Continued attempting to get uart to work and failed. Created new pin out diagram
2026-02-13 | Check-in | 10:40:00 | 14:30:00 | 3:50:00 | Check-in 8: Met with group & Tyler to demo current status of beta build; Still couldn't get NPK working :(
2026-02-15 | Beta Build | 20:25:00 | 21:00:00 | 0:35:00 | Implemented ability to toggle autoschedule in main depending on different topic messages
2026-02-16 | Beta Build | 11:15:00 | 12:41:00 | 1:26:00 | Started testing NPK AND IT STILL DOESN'T WORK OH MY GOD
2026-02-17 | Beta Build | 10:40:00 | 12:48:00 | 2:08:00 | Got together as a goup and began planning phsyical layout of board
2026-02-17 | Beta Build | 13:47:00 | 17:47:00 | 4:00:00 | Finishing planning out board and began soldering. Got and tested LED and photoresistor
2026-02-19 | Beta Build | 13:40:00 | 20:09:00 | 6:29:00 | Soldered everything together, tested everything, and then burnt out everything while trying to test it all
2026-02-20 | Beta Build | 11:00:00 | 17:06:00 | 6:06:00 | Figured out what actually broke and fixed board with Sabrina. Replaced falling out wires with headers
2026-03-02 | Beta Build | 10:00:00 | 12:00:00 | 2:00:00 | Check-in 9: Met with Tyler to demo beta build
2026-03-03 | Release Candidate | 11:00:00 | 12:52:00 | 1:52:00 | Help Nick merge database into main; Made it so http requests are tried until sent for at least 5 times. Updated project issues.
2026-03-10 | Release Candidate | 10:40:00 | 13:28:00 | 2:48:00 | Discussed what needed to be done and assigned tasks regarding NPK and PCB; Talked through 3D and decided on what structures to go through with; set up documentation and delegated when and who needed to complete what
2026-03-10 | Release Candidate | 16:36:00 | 17:02:00 | 0:26:00 | Started integrating fixed NPK code into main
2026-03-10 | Release Candidate | 20:02:00 | 22:06:00 | 2:04:00 | Finished integrating fixed NPK code into main
2026-03-12 | Instructor Meeting | 11:40:00 | 12:00:00 | 0:20:00 | Met up with group and instructor to demonstrate and discuss current plans for the permenant housing/hardware for the project.
2026-03-12 | Check-in | 12:00:00 | 12:20:00 | 0:20:00 | Check-in 9: Met with tyler to show integration of current database changes into main, communication error handling, NPK integration, the current arrival and soldering of the new PCB, and the plans for the 3D printed housing.
2026-03-12 | Release Candidate | 12:20:00 | 13:39:00 | 1:19:00 | Tested NPK sensor and confirmed it worked with integrated main code. Then proceeded to complete Beta Tests notes.
2026-03-13 | Release Candidate | 18:50:00 | 21:45:00 | 2:55:00 | Worked on onshape design
2026-03-14 | Release Candidate | 12:00:00 | 15:45:00 | 3:45:00 | Worked on onshape design
2026-03-24 | Release Candidate | 11:50:00 | 13:00:00 | 1:10:00 | Brought in new PCB's and components; Discussed what should be done for the 3D CAD, work left to be done, and future meetings
2026-03-25 | Release Candidate | 9:55:00 | 11:26:00 | 1:31:00 | Worked on onshape design
2026-03-25 | Release Candidate | 15:00:00 | 16:05:00 | 1:05:00 | Worked on onshape design
2026-03-26 | Release Candidate | 10:40:00 | 12:50:00 | 2:10:00 | Soldered header pins on newly arrived PCB
2026-03-28 | Release Candidate | 10:45:00 | 15:42:00 | 4:57:00 | Fixing onshape design
2026-03-31 | Release Candidate | 10:40:00 | 15:53:00 | 5:13:00 | Helped merge and fix inconsistied encountered with new handshake protocols and app., test PCB, adjusted 3D model to fit printer
2026-04-02 | Release Candidate/Instructor Meeting | 9:35:00 | 16:19:00 | 6:44:00 | Had indstructor meeting at 12; Began integrating final build for TA demo, helped drill holes in water containers, threaded pipes through, soldered new PCB
2026-04-03 | Check-in | 10:35:00 | 11:30:00 | 0:55:00 | Check-in 10: Met with Tyler to show integration of current NPK changes, app changes and the PCB
2026-04-14 | Production Release | 10:36:00 | 11:15:00 | 0:39:00 | Modify added task changes to remove bugs
2026-04-14 | Production Release | 13:00:00 | 15:23:00 | 2:23:00 | Tested and adjusted Fernando's code with app and database. Discusses what was left that needs to be completed.
 |  |  |  | 0:00:00
 |  |  |  | 0:00:00
 |  |  |  | 0:00:00
 |  |  |  | 0:00:00
 |  |  |  | 0:00:00
 |  |  |  | 0:00:00
 |  |  |  | 0:00:00
 |  |  |  | 0:00:00
 |  |  |  | 0:00:00
 |  |  |  | 0:00:00
 |  |  |  | 0:00:00
 |  |  |  | 0:00:00
 |  |  |  | 0:00:00
 |  |  |  | 0:00:00
 |  |  |  | 0:00:00
 |  |  |  | 0:00:00
 |  |  |  | 0:00:00
 |  |  |  | 0:00:00
 |  |  |  | 0:00:00
 |  |  |  | 0:00:00
 |  |  |  | 0:00:00
 |  |  |  | 0:00:00
 |  |  |  | 0:00:00
 |  |  |  | 0:00:00
 |  |  |  | 0:00:00
 |  |  |  | 0:00:00
 |  |  |  | 0:00:00
 |  |  |  | 0:00:00
 |  |  |  | 0:00:00
 |  |  |  | 0:00:00
 |  |  |  | 0:00:00
 |  |  |  | 0:00:00
 |  |  |  | 0:00:00
 |  |  |  | 0:00:00
 |  |  |  | 0:00:00
 |  |  |  | 0:00:00
 |  |  |  | 0:00:00
 |  |  |  | 0:00:00
 |  |  |  | 0:00:00
 |  |  |  | 0:00:00
 |  |  |  | 0:00:00
 |  |  |  | 0:00:00
 |  |  |  | 0:00:00
 |  |  |  | 0:00:00
 |  |  |  | 0:00:00
 |  |  |  | 0:00:00
 |  |  |  | 0:00:00
 |  |  |  | 0:00:00
 |  |  |  | 0:00:00
 |  |  |  | 0:00:00
 |  |  |  | 0:00:00
 |  |  |  | 0:00:00
 |  |  |  | 0:00:00
 |  |  |  | 0:00:00
 |  |  |  | 0:00:00
 |  |  |  | 0:00:00
 |  |  |  | 0:00:00
 |  |  |  | 0:00:00
 |  |  |  | 0:00:00
 |  |  |  | 0:00:00
 |  |  |  | 0:00:00
 |  |  |  | 0:00:00
 |  |  |  | 0:00:00
 |  |  |  | 0:00:00
 |  |  |  | 0:00:00
 |  |  |  | 0:00:00
 |  |  |  | 0:00:00
 |  |  |  | 0:00:00
 |  |  |  | 0:00:00
 |  |  |  | 0:00:00
 |  |  |  | 0:00:00
 |  |  |  | 0:00:00
 |  |  |  | 0:00:00
 |  |  |  | 0:00:00
 |  |  |  | 0:00:00
 |  |  |  | 0:00:00
 |  |  |  | 0:00:00
 |  |  |  | 0:00:00
 |  |  |  | 0:00:00
 |  |  |  | 0:00:00
 |  |  |  | 0:00:00
 |  |  |  | 0:00:00
 |  |  |  | 0:00:00
 |  |  |  | 0:00:00
 |  |  |  | 0:00:00
 |  |  |  | 0:00:00
 |  |  |  | 0:00:00
 |  |  |  | 0:00:00
 |  |  |  | 0:00:00
 |  |  |  | 0:00:00
 |  |  |  | 0:00:00
 |  |  |  | 0:00:00
 |  |  |  | 0:00:00
 |  |  |  | 0:00:00
 |  |  |  | 0:00:00
 |  |  |  | 0:00:00
 |  |  |  | 0:00:00
 |  |  |  | 0:00:00
 |  |  |  | 0:00:00
 |  |  |  | 0:00:00
 |  |  |  | 0:00:00
 |  |  |  | 0:00:00
 |  |  |  | 0:00:00
 |  |  |  | 0:00:00
 |  |  |  | 0:00:00
 |  |  |  | 0:00:00
 |  |  |  | 0:00:00
 |  |  |  | 0:00:00
 |  |  |  | 0:00:00
 |  |  |  | 0:00:00
 |  |  |  | 0:00:00
 |  |  |  | 0:00:00
 |  |  |  | 0:00:00
 |  |  |  | 0:00:00
 |  |  |  | 0:00:00
 |  |  |  | 0:00:00

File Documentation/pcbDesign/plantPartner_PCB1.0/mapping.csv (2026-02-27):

Footprint | Part Value | LCSC Part
C1,C2 | 2 | 22uF
C3 | 1 | 10uF
C4 | 1 | 0.1uF
D1,D2,D3,D5,D6,D10,D11 | 7 | LED
D4,D7 | 2 | 1N400x
D8,D9 | 2 | SS14
IC1 | 1 | MPM3610
J1,J2,J3,J16,J21,J22 | 6 | Conn_01x04
J18,J30 | 2 | Screw_Terminal_01x02
J19 | 1 | Barrel_Jack
J23,J26,J27,J28 | 4 | Conn_01x01
J4 | 1 | Screw_Terminal
J5,J11,J29 | 3 | Conn_01x02
J6,J10 | 2 | Screw_Terminal_01x03
J7,J9,J12,J13,J14,J15,J17,J24,J25 | 9 | Conn_01x03
J8,J20 | 2 | Conn_02x04_Top_Bottom
K1,K2 | 2 | SRD-05VDC-SL-C
Q1,Q2 | 2 | PNP
Q4 | 1 | AO3400A
R1,R2 | 2 | 100k
R11 | 1 | 120
R13,R18 | 2 | 500
R15,R20 | 2 | 470
R25 | 1 | 100
R3 | 1 | 18.7k
R4,R5,R6,R7,R14,R19,R27 | 7 | 10k
R8,R12,R16,R17,R21,R22,R23,R24,R26 | 9 | 1k
R9,R10 | 2 | 20k
U1,U4 | 2 | EL357N-G
U2 | 1 | MAX485
U3 | 1 | ESP32-DEVKIT-V1

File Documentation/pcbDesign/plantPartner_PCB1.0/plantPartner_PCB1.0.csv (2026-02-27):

Reference | Qty | Value | DNP | Exclude from BOM | Exclude from Board | Footprint | Datasheet
C1,C2 | 2 | 22uF |  |  |  | Capacitor_SMD:C_0201_0603Metric | ~
C3 | 1 | 10uF |  |  |  | Capacitor_SMD:C_0201_0603Metric | ~
C4 | 1 | 0.1uF |  |  |  | Capacitor_SMD:C_0201_0603Metric | ~
D1,D2,D3,D5,D6,D10,D11 | 7 | LED |  |  |  | LED_SMD:LED_0201_0603Metric | ~
D4,D7 | 2 | 1N400x |  |  |  | Diode_THT:D_A-405_P7.62mm_Horizontal | ~
D8,D9 | 2 | SS14 |  |  |  | Diode_SMD:D_SMA | ~
IC1 | 1 | MPM3610 |  |  |  | MPM3610:MPM3610
J1,J2,J3,J16,J21,J22 | 6 | Conn_01x04 |  |  |  | Connector_PinHeader_2.54mm:PinHeader_1x04_P2.54mm_Vertical | ~
J4 | 1 | Screw_Terminal |  |  |  | TerminalBlock_Phoenix:TerminalBlock_Phoenix_MKDS-1,5-4-5.08_1x04_P5.08mm_Horizontal | ~
J5,J11,J29 | 3 | Conn_01x02 |  |  |  | Connector_PinHeader_2.54mm:PinHeader_1x02_P2.54mm_Vertical | ~
J6,J10 | 2 | Screw_Terminal_01x03 |  |  |  | TerminalBlock_Phoenix:TerminalBlock_Phoenix_MKDS-1,5-3-5.08_1x03_P5.08mm_Horizontal | ~
J7,J9,J12,J13,J14,J15,J17,J24,J25 | 9 | Conn_01x03 |  |  |  | Connector_PinHeader_2.54mm:PinHeader_1x03_P2.54mm_Vertical | ~
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

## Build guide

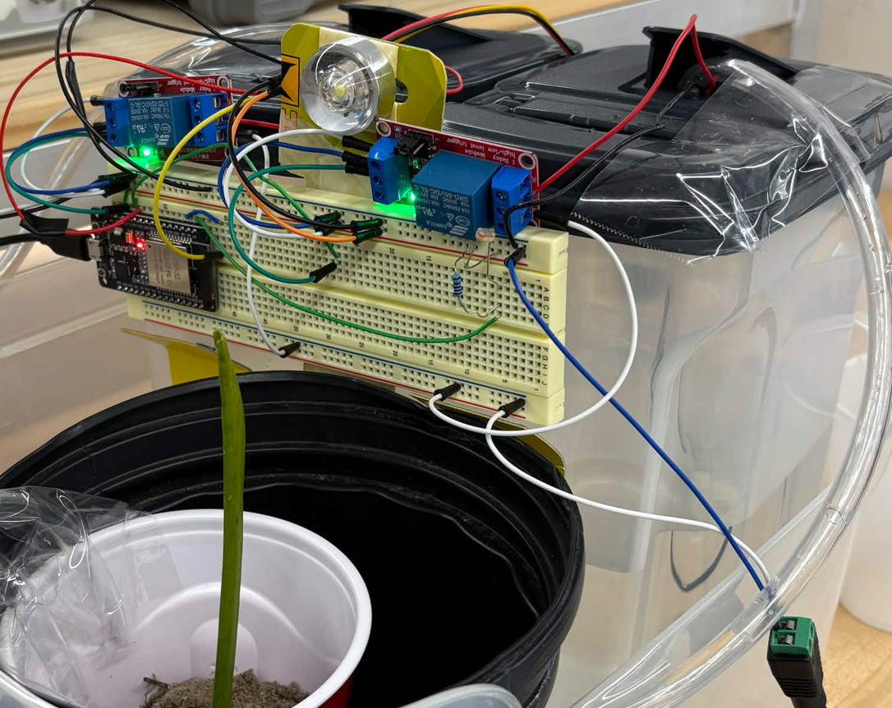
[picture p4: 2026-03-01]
Documentation/Circuits/BetaBuild_NewBreadboard.png

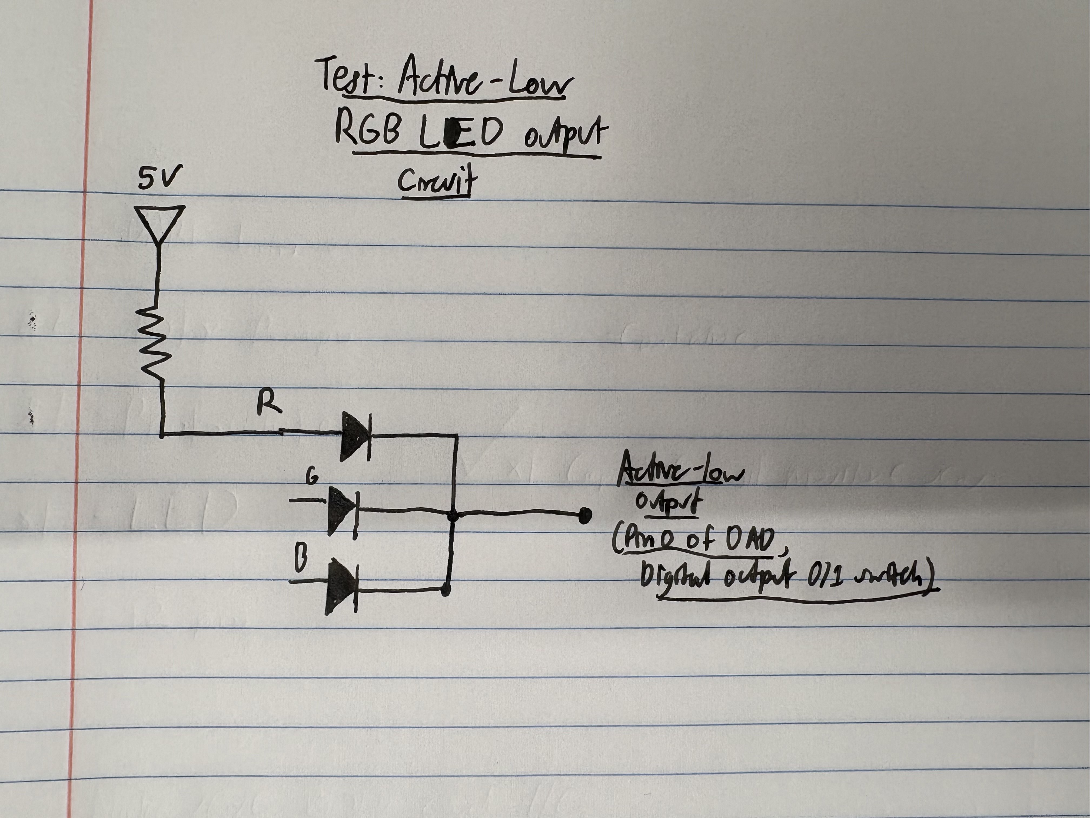
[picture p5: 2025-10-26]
Documentation/Diagrams/PreAlphaBuild_Circuit_ExternalLED.jpg

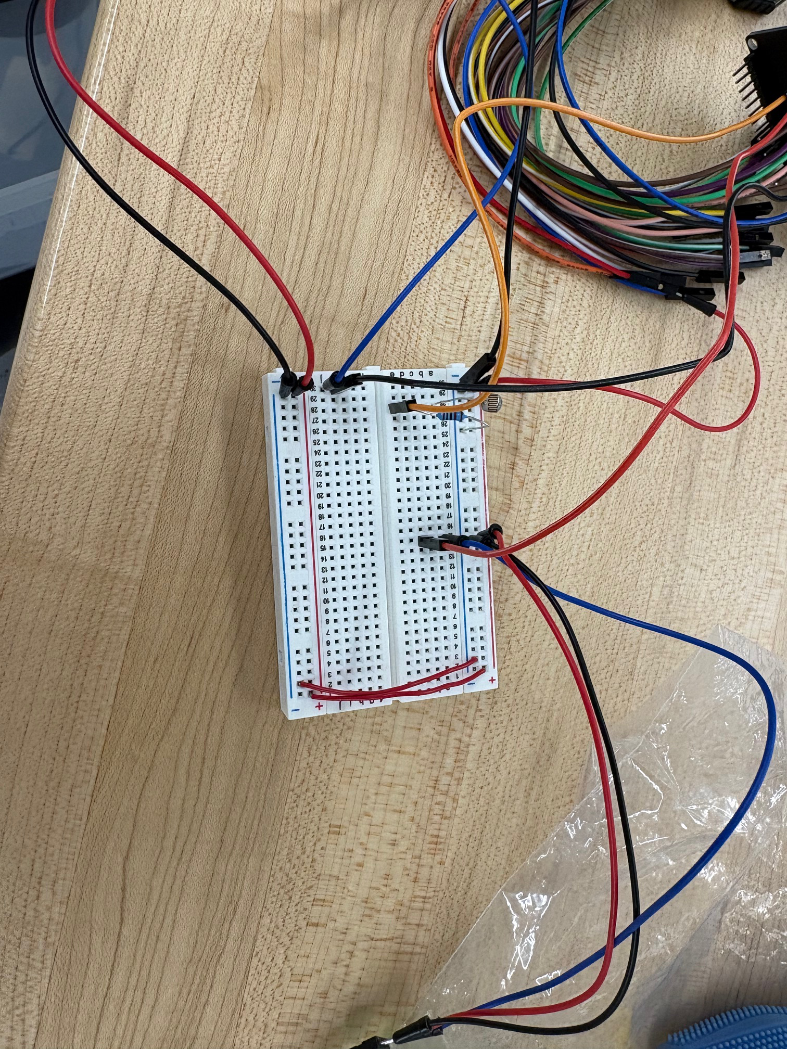
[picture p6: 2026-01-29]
Documentation/Circuits/AlphaBuild_NewBreadBoard.jpeg

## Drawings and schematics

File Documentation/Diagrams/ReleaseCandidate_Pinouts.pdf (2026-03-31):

# EEE.ttEiii.Ii

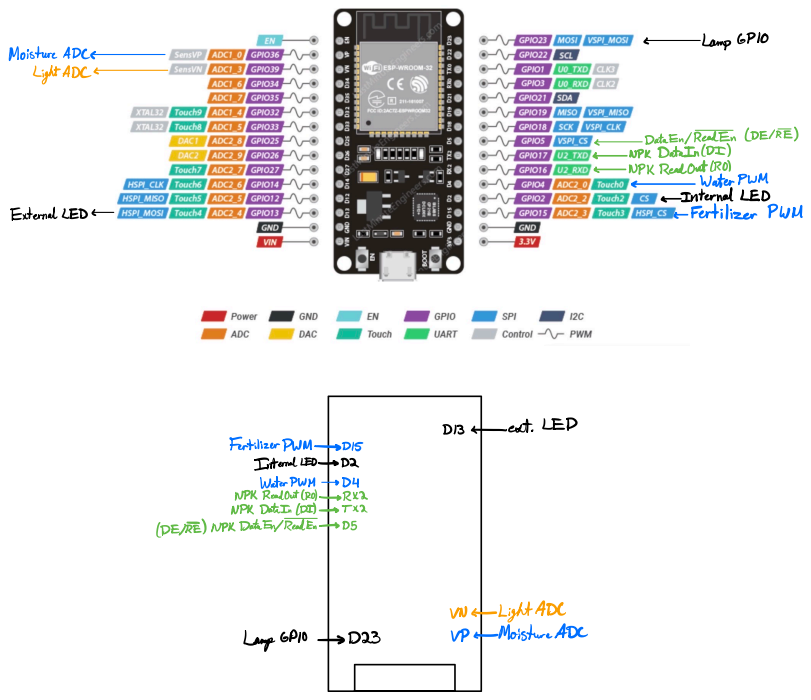
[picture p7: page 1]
LampGPIO; Moistine; ExternalLED; fertilizePWM; extLED; n.itiiEIIIEIIII; Ypito.MILIDc

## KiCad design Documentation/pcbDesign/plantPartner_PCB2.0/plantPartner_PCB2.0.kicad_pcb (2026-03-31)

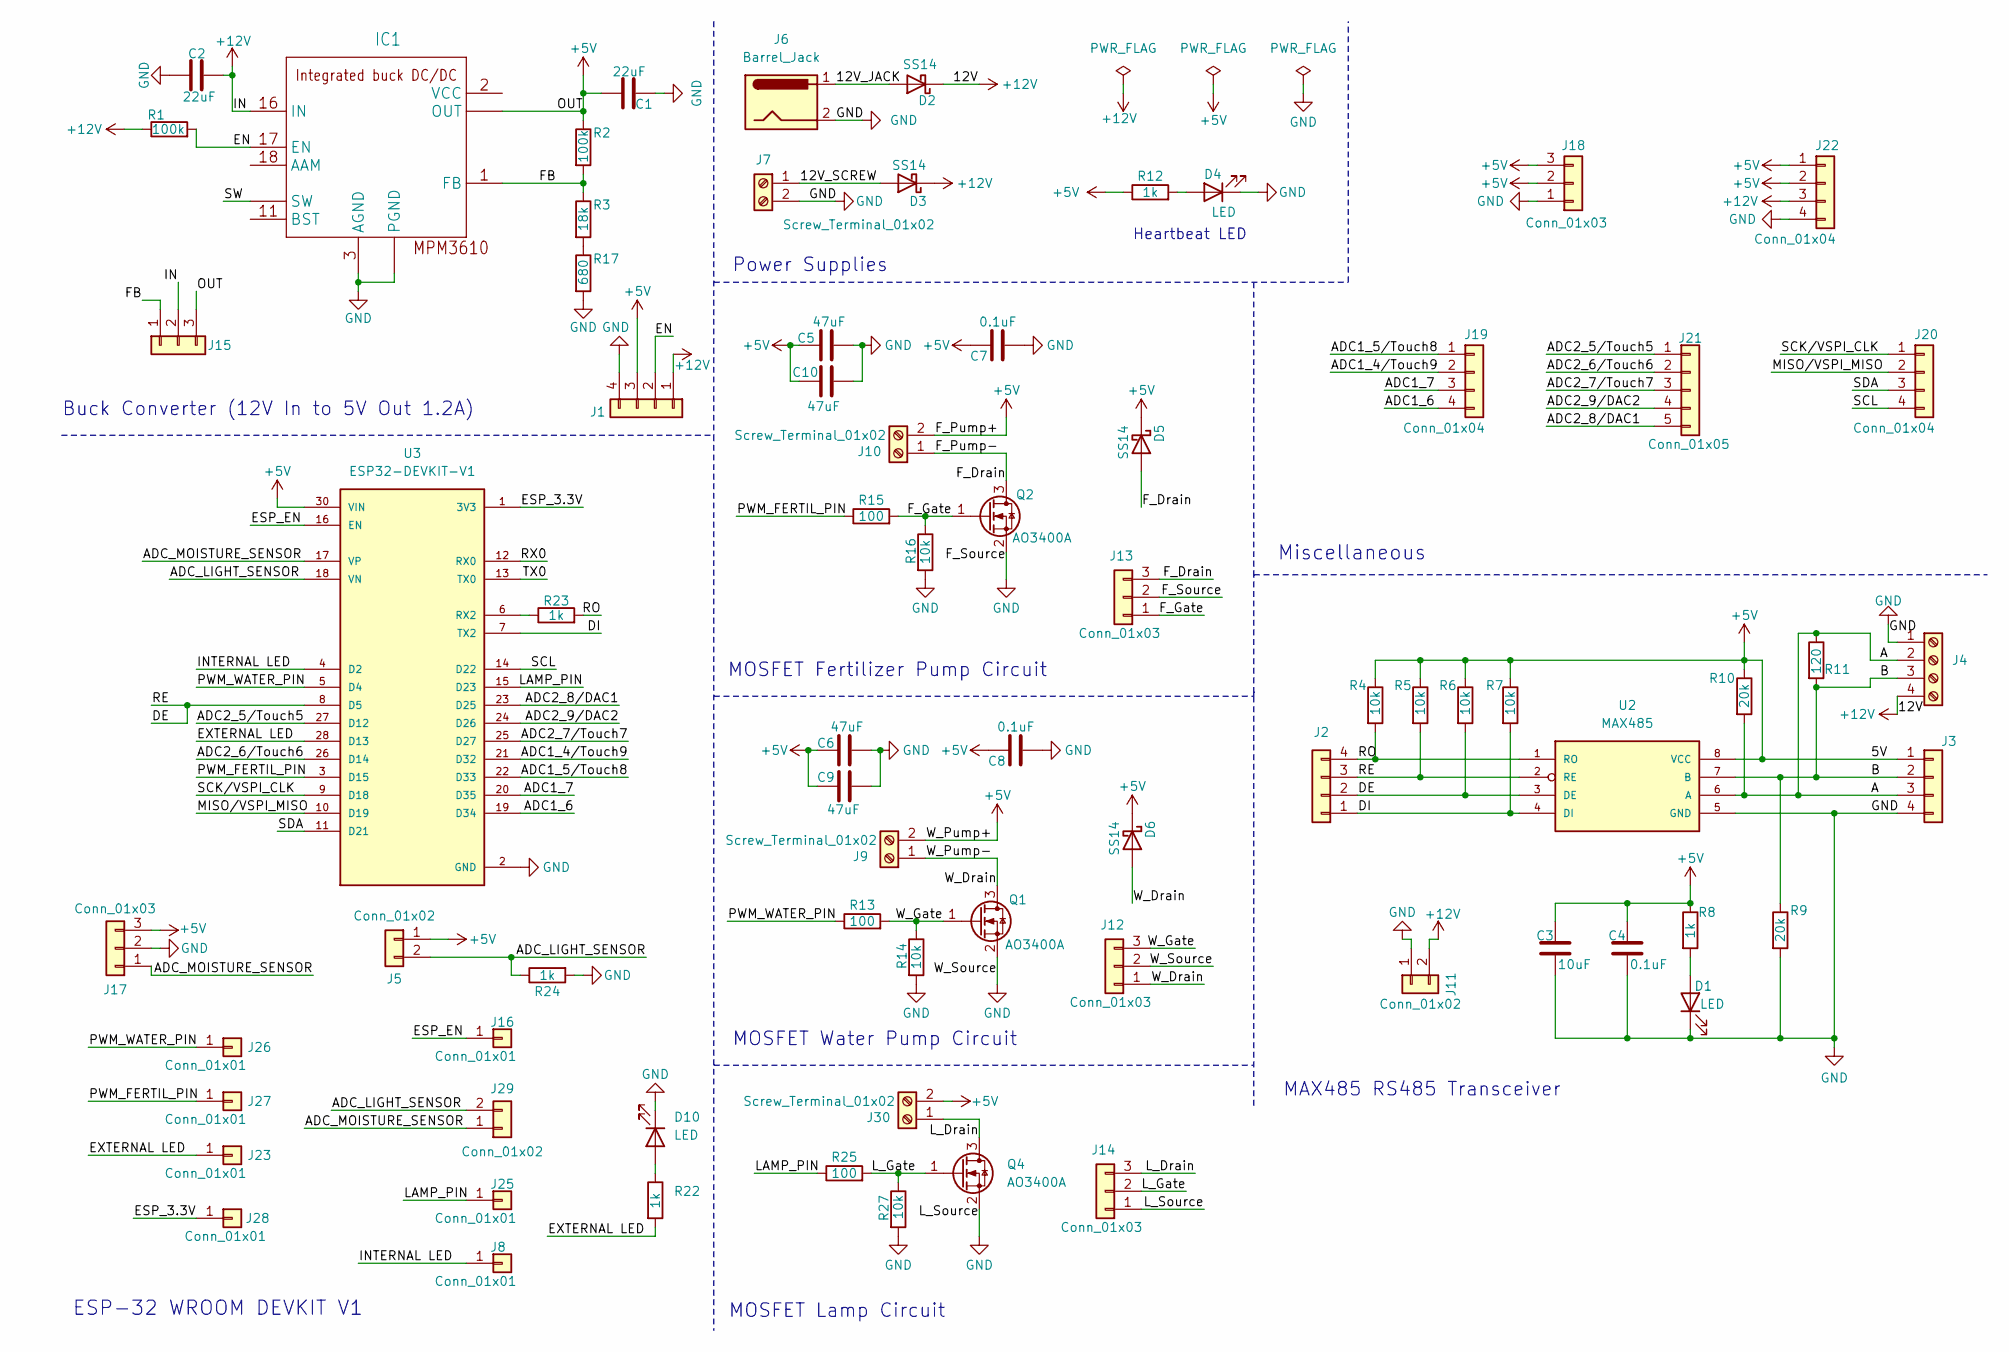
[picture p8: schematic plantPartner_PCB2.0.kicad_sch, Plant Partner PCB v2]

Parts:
C1, C2: 22uF; C_0603_1608Metric
C3: 10uF; C_0402_1005Metric
C4: 0.1uF; C_0402_1005Metric
C5, C6, C9, C10: 47uF; C_0805_2012Metric
C7, C8: 0.1uF; C_0603_1608Metric
D1, D4, D10: LED; LED_0603_1608Metric
D2, D3, D5, D6: SS14; D_SMA
IC1: MPM3610
J1, J2, J3, J19, J20, J22: Conn_01x04; PinHeader_1x04_P2.54mm_Vertical
J4: Screw_Terminal_01x04; TerminalBlock_Phoenix_MPT-0,5-4-2.54_1x04_P2.54mm_Horizontal
J5, J11, J29: Conn_01x02; PinHeader_1x02_P2.54mm_Vertical
J6: Barrel_Jack; BarrelJack_GCT_DCJ200-10-A_Horizontal
J7, J9, J10, J30: Screw_Terminal_01x02; TerminalBlock_Phoenix_MPT-0,5-2-2.54_1x02_P2.54mm_Horizontal
J8, J16, J23, J25, J26, J27, J28: Conn_01x01; PinHeader_1x01_P2.54mm_Vertical
J12, J13, J14, J15, J17, J18: Conn_01x03; PinHeader_1x03_P2.54mm_Vertical
J21: Conn_01x05; PinHeader_1x05_P2.54mm_Vertical
Q1, Q2, Q4: AO3400A; SOT-23
R1, R2: 100k; R_0402_1005Metric
R3: 18k; R_0603_1608Metric
R4, R5, R6, R7, R14, R16, R27: 10k; R_0402_1005Metric
R8, R12, R22, R23, R24: 1k; R_0402_1005Metric
R9, R10: 20k; R_0402_1005Metric
R11: 120; R_0402_1005Metric
R13, R15, R25: 100; R_0402_1005Metric
R17: 680; R_0603_1608Metric
U2: MAX485; SO08
U3: ESP32-DEVKIT-V1; MODULE_ESP32_DEVKIT_V1; PARTREV N/A

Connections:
+5V: C1.1, C3.1, C4.1, C5.1, C6.1, C7.1, C8.1, C9.1, C10.1, D5.1 (K), D6.1 (K), IC1.7 (OUT), IC1.8 (OUT), IC1.9 (OUT), J1.3, J3.1, J5.1, J9.2, J10.2, J15.3, J17.3, J18.2, J18.3, J22.1, J22.2, J30.2, R2.1, R4.1, R5.1, R6.1, R7.1, R8.1, R10.1, R12.1, U2.8 (VCC), U3.30 (VIN)
+12V: C2.1, D2.1 (K), D3.1 (K), IC1.16 (IN), J1.1, J4.4, J11.2, J15.2, J22.3, R1.1
/12V_JACK: D2.2 (A), J6.1
/12V_SCREW: D3.2 (A), J7.1
/A: J3.3, J4.2, R10.2, R11.1, U2.6 (A)
/ADC1_4/Touch9: J19.2, U3.21 (D32)
/ADC1_5/Touch8: J19.1, U3.22 (D33)
/ADC1_6: J19.4, U3.19 (D34)
/ADC1_7: J19.3, U3.20 (D35)
/ADC2_5/Touch5: J21.1, U3.27 (D12)
/ADC2_6/Touch6: J21.2, U3.26 (D14)
/ADC2_7/Touch7: J21.3, U3.25 (D27)
/ADC2_8/DAC1: J21.5, U3.23 (D25)
/ADC2_9/DAC2: J21.4, U3.24 (D26)
/ADC_LIGHT_SENSOR: J5.2, J29.2, R24.1, U3.18 (VN)
/ADC_MOISTURE_SENSOR: J17.1, J29.1, U3.17 (VP)
/B: J3.2, J4.3, R9.1, R11.2, U2.7 (B)
/DE: J2.2, J2.3, R5.2, R6.2, U2.2 (RE), U2.3 (DE), U3.8 (D5)
/DI: J2.1, R7.2, U2.4 (DI), U3.7 (TX2)
/EN: IC1.17 (EN), J1.2, R1.2
/ESP_3.3V: J28.1, U3.1 (3V3)
/ESP_EN: J16.1, U3.16 (EN)
/EXTERNAL LED: J23.1, R22.2, U3.28 (D13)
/FB: IC1.1 (FB), J15.1, R2.2, R3.1
/F_Drain: D5.2 (A), J10.1, J13.3, Q2.3 (D)
/F_Gate: J13.1, Q2.1 (G), R15.2, R16.1
/INTERNAL LED: J8.1, U3.4 (D2)
/LAMP_PIN: J25.1, R25.1, U3.15 (D23)
/L_Drain: J14.3, J30.1, Q4.3 (D)
/L_Gate: J14.2, Q4.1 (G), R25.2, R27.1
/MISO/VSPI_MISO: J20.2, U3.10 (D19)
/PWM_FERTIL_PIN: J27.1, R15.1, U3.3 (D15)
/PWM_WATER_PIN: J26.1, R13.1, U3.5 (D4)
/RO: J2.4, R4.2, R23.2, U2.1 (RO)
/RX0: U3.12 (RX0)
/SCK/VSPI_CLK: J20.1, U3.9 (D18)
/SCL: J20.4, U3.14 (D22)
/SDA: J20.3, U3.11 (D21)
/SW: IC1.4 (SW), IC1.5 (SW), IC1.6 (SW)
/TX0: U3.13 (TX0)
/W_Drain: D6.2 (A), J9.1, J12.1, Q1.3 (D)
/W_Gate: J12.3, Q1.1 (G), R13.2, R14.1
GND: C1.2, C2.2, C3.2, C4.2, C5.2, C6.2, C7.2, C8.2, C9.2, C10.2, D1.1 (K), D4.1 (K), D10.1 (K), IC1.3 (AGND), IC1.12 (PGND), IC1.13 (PGND), IC1.14 (PGND), J1.4, J3.4, J4.1, J6.2, J7.2, J11.1, J12.2, J13.2, J14.1, J17.2, J18.1, J22.4, Q1.2 (S), Q2.2 (S), Q4.2 (S), R9.2, R14.2, R16.2, R17.2, R24.2, R27.2, U2.5 (GND), U3.2 (GND), U3.29 (GND)
unnamed: D1.2 (A), R8.2
unnamed: D4.2 (A), R12.2
unnamed: D10.2 (A), R22.1
unnamed: R3.2, R17.1
unnamed: R23.1, U3.6 (RX2)

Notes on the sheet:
Heartbeat LED
Power Supplies
ESP-32 WROOM DEVKIT V1
Miscellaneous
MAX485 RS485 Transceiver
Buck Converter (12V In to 5V Out 1.2A)
MOSFET Water Pump Circuit
MOSFET Fertilizer Pump Circuit
MOSFET Lamp Circuit

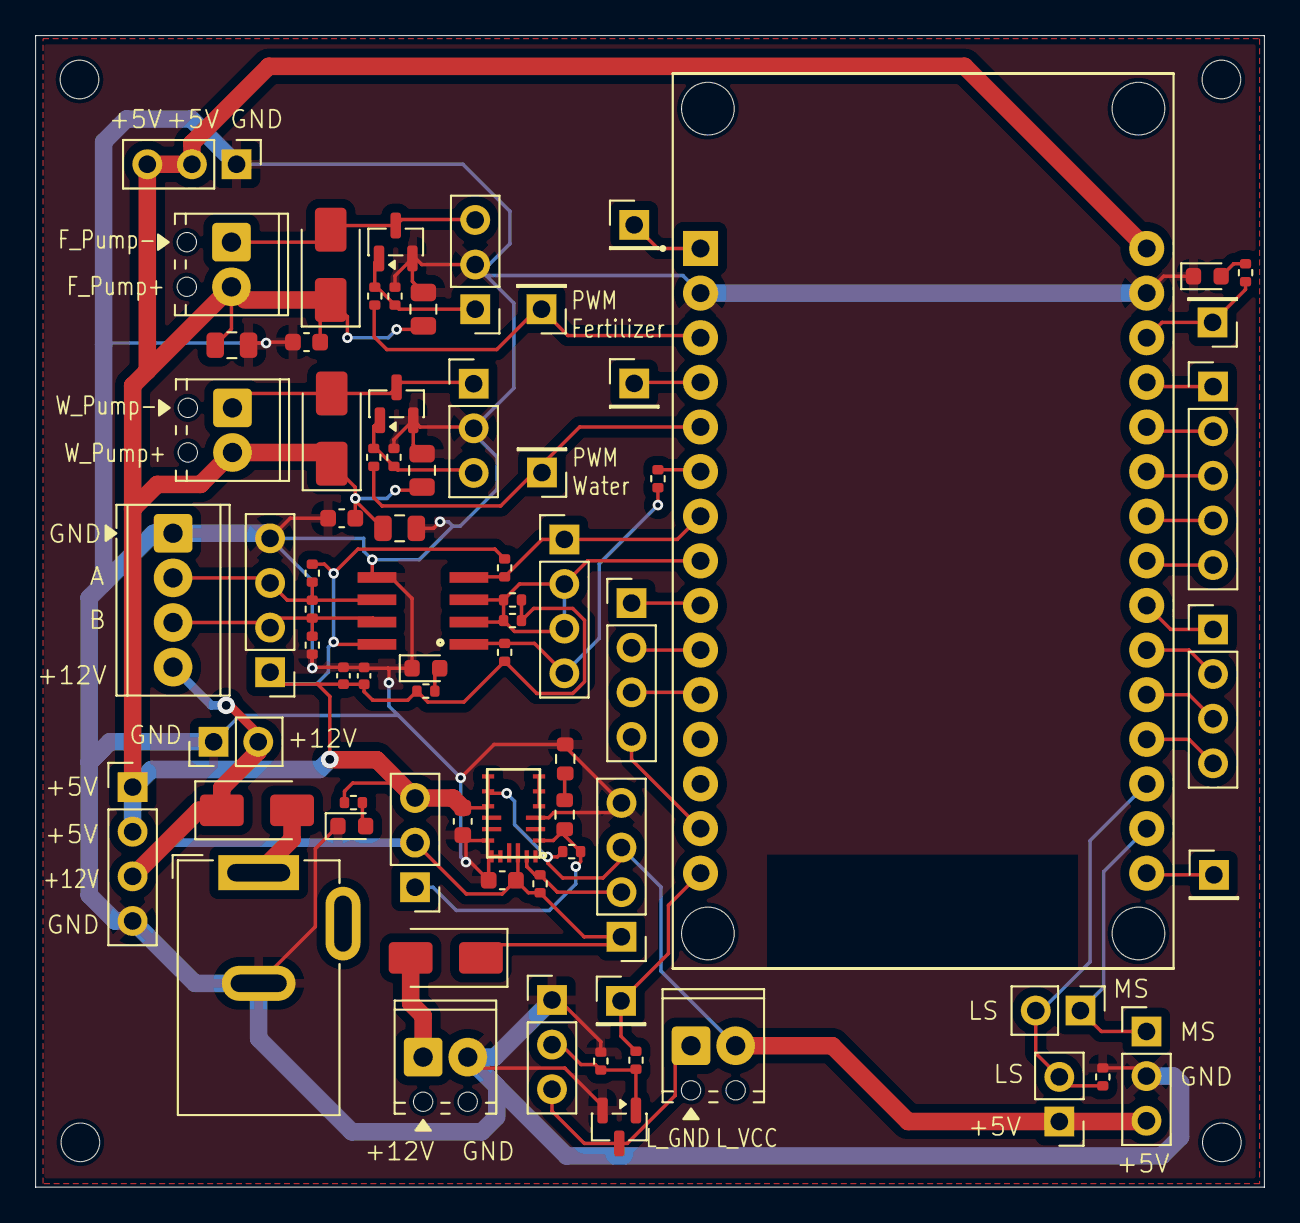
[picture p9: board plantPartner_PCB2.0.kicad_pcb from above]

Board: 2 copper layers, 70.0 x 65.5 mm, 74 parts (0 on the bottom side), 46 nets.

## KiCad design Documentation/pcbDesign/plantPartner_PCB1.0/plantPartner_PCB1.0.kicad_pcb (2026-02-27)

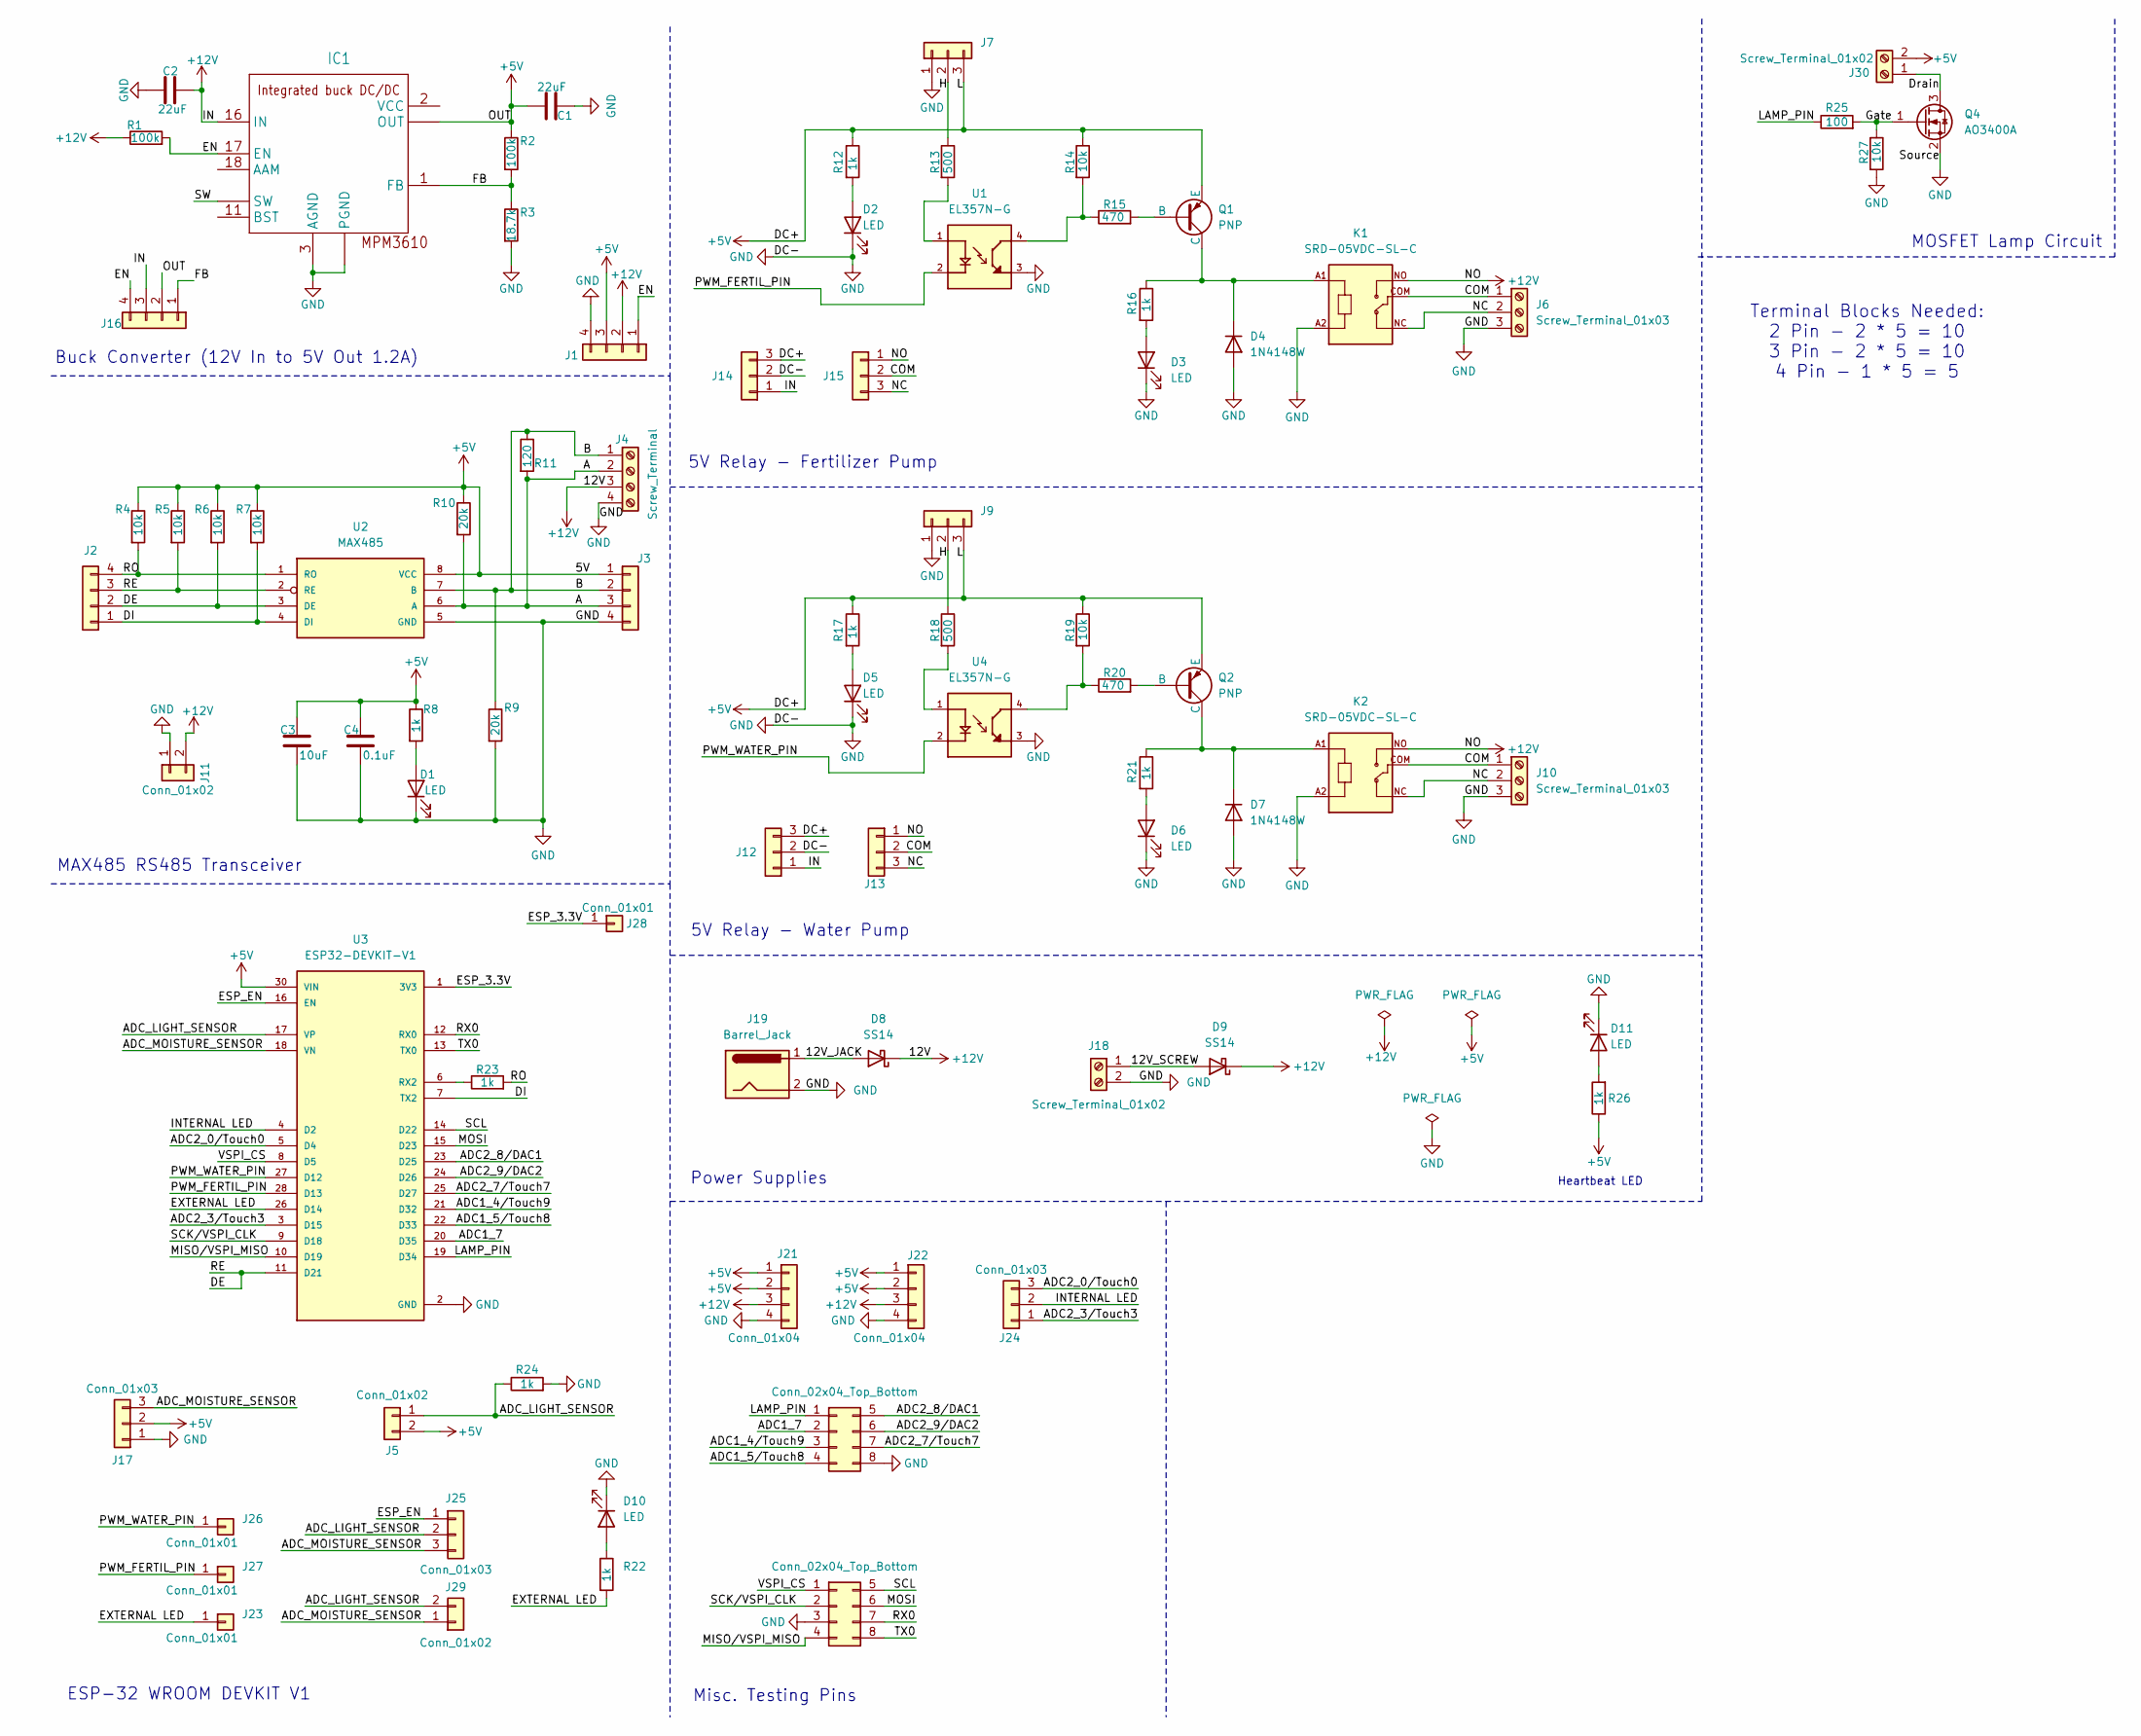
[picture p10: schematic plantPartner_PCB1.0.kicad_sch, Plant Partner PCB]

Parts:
C1, C2: 22uF; C_0603_1608Metric
C3: 10uF; C_0402_1005Metric
C4: 0.1uF; C_0402_1005Metric
D1, D2, D3, D5, D6, D10, D11: LED; LED_0603_1608Metric
D4, D7: 1N4148W; D_SOD-123
D8, D9: SS14; D_SMA
IC1: MPM3610
J1, J2, J3, J16, J21, J22: Conn_01x04; PinHeader_1x04_P2.54mm_Vertical
J4: Screw_Terminal; TerminalBlock_Phoenix_MPT-0,5-4-2.54_1x04_P2.54mm_Horizontal
J5, J11, J29: Conn_01x02; PinHeader_1x02_P2.54mm_Vertical
J6, J10: Screw_Terminal_01x03; TerminalBlock_Phoenix_MPT-0,5-3-2.54_1x03_P2.54mm_Horizontal
J7, J9, J12, J13, J14, J15, J17, J24, J25: Conn_01x03; PinHeader_1x03_P2.54mm_Vertical
J8, J20: Conn_02x04_Top_Bottom; PinHeader_2x04_P2.54mm_Vertical
J18, J30: Screw_Terminal_01x02; TerminalBlock_Phoenix_MPT-0,5-2-2.54_1x02_P2.54mm_Horizontal
J19: Barrel_Jack; BarrelJack_GCT_DCJ200-10-A_Horizontal
J23, J26, J27, J28: Conn_01x01; PinHeader_1x01_P2.54mm_Vertical
K1, K2: SRD-05VDC-SL-C; RELAY_SRD-05VDC-SL-C
Q1, Q2: PNP; TO-92
Q4: AO3400A; SOT-23
R1, R2: 100k; R_0402_1005Metric
R3: 18.7k; R_0603_1608Metric
R4, R5, R6, R7, R14, R19, R27: 10k; R_0402_1005Metric
R8, R12, R16, R17, R21, R22, R23, R24, R26: 1k; R_0402_1005Metric
R9, R10: 20k; R_0402_1005Metric
R11: 120; R_0402_1005Metric
R13, R18: 500; R_0603_1608Metric
R15, R20: 470; R_0402_1005Metric
R25: 100; R_0402_1005Metric
U1, U4: EL357N-G; OPTO_EL357N-G; PARTREV 6
U2: MAX485; SO08
U3: ESP32-DEVKIT-V1; MODULE_ESP32_DEVKIT_V1; PARTREV N/A

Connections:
+5V: C1.1, C3.1, C4.1, IC1.7 (OUT), IC1.8 (OUT), IC1.9 (OUT), J1.3, J3.1, J5.2, J7.3, J9.3, J12.3, J14.3, J16.2, J17.2, J21.1, J21.2, J22.1, J22.2, J30.2, Q1.3 (E), Q2.3 (E), R2.1, R4.1, R5.1, R6.1, R7.1, R8.1, R10.1, R12.1, R14.1, R17.1, R19.1, R26.1, U2.8 (VCC), U3.30 (VIN)
+12V: C2.1, D8.1 (K), D9.1 (K), IC1.16 (IN), J1.2, J4.3, J11.2, J12.1, J13.1, J14.1, J15.1, J16.3, J21.3, J22.3, K1.NO, K2.NO, R1.1
/12V_JACK: D8.2 (A), J19.1
/12V_SCREW: D9.2 (A), J18.1
/A: J3.3, J4.2, R10.2, R11.2, U2.6 (A)
/ADC1_4/Touch9: J20.3, U3.21 (D32)
/ADC1_5/Touch8: J20.4, U3.22 (D33)
/ADC1_7: J20.2, U3.20 (D35)
/ADC2_0/Touch0: J24.3, U3.5 (D4)
/ADC2_3/Touch3: J24.1, U3.3 (D15)
/ADC2_7/Touch7: J20.7, U3.25 (D27)
/ADC2_8/DAC1: J20.5, U3.23 (D25)
/ADC2_9/DAC2: J20.6, U3.24 (D26)
/ADC_LIGHT_SENSOR: J5.1, J25.2, J29.2, R24.1, U3.17 (VP)
/ADC_MOISTURE_SENSOR: J17.3, J25.3, J29.1, U3.18 (VN)
/B: J3.2, J4.1, R9.1, R11.1, U2.7 (B)
/COM: J6.1, J10.1, J13.2, J15.2, K1.COM, K2.COM
/DE: J2.2, J2.3, R5.2, R6.2, U2.2 (RE), U2.3 (DE), U3.11 (D21)
/DI: J2.1, R7.2, U2.4 (DI), U3.7 (TX2)
/Drain: J30.1, Q4.3 (D)
/EN: IC1.17 (EN), J1.1, J16.4, R1.2
/ESP_3.3V: J28.1, U3.1 (3V3)
/ESP_EN: J25.1, U3.16 (EN)
/EXTERNAL LED: J23.1, R22.2, U3.26 (D14)
/FB: IC1.1 (FB), J16.1, R2.2, R3.1
/Gate: Q4.1 (G), R25.2, R27.1
/H: J7.2, J9.2, R13.1, R18.1
/INTERNAL LED: J24.2, U3.4 (D2)
/LAMP_PIN: J20.1, R25.1, U3.19 (D34)
/MISO/VSPI_MISO: J8.4, U3.10 (D19)
/MOSI: J8.6, U3.15 (D23)
/NC: J6.2, J10.2, J13.3, J15.3, K1.NC, K2.NC
/PWM_FERTIL_PIN: J27.1, U1.2, U3.28 (D13)
/PWM_WATER_PIN: J26.1, U3.27 (D12), U4.2
/RO: J2.4, R4.2, R23.2, U2.1 (RO)
/RX0: J8.7, U3.12 (RX0)
/SCK/VSPI_CLK: J8.2, U3.9 (D18)
/SCL: J8.5, U3.14 (D22)
/SW: IC1.4 (SW), IC1.5 (SW), IC1.6 (SW)
/TX0: J8.8, U3.13 (TX0)
/VSPI_CS: J8.1, U3.8 (D5)
GND: C1.2, C2.2, C3.2, C4.2, D1.1 (K), D2.1 (K), D3.1 (K), D4.2 (A), D5.1 (K), D6.1 (K), D7.2 (A), D10.1 (K), D11.1 (K), IC1.3 (AGND), IC1.12 (PGND), IC1.13 (PGND), IC1.14 (PGND), J1.4, J3.4, J4.4, J6.3, J7.1, J8.3, J9.1, J10.3, J11.1, J12.2, J14.2, J17.1, J18.2, J19.2, J20.8, J21.4, J22.4, K1.A2, K2.A2, Q4.2 (S), R3.2, R9.2, R24.2, R27.2, U1.3, U2.5 (GND), U3.2 (GND), U3.29 (GND), U4.3
unnamed: D1.2 (A), R8.2
unnamed: D2.2 (A), R12.2
unnamed: D3.2 (A), R16.2
unnamed: D4.1 (K), K1.A1, Q1.1 (C), R16.1
unnamed: D5.2 (A), R17.2
unnamed: D6.2 (A), R21.2
unnamed: D7.1 (K), K2.A1, Q2.1 (C), R21.1
unnamed: D10.2 (A), R22.1
unnamed: D11.2 (A), R26.2
unnamed: Q1.2 (B), R15.2
unnamed: Q2.2 (B), R20.2
unnamed: R13.2, U1.1
unnamed: R14.2, R15.1, U1.4
unnamed: R18.2, U4.1
unnamed: R19.2, R20.1, U4.4
unnamed: R23.1, U3.6 (RX2)

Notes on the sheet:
Buck Converter (12V In to 5V Out 1.2A)
ESP-32 WROOM DEVKIT V1
Misc. Testing Pins
5V Relay - Fertilizer Pump
Power Supplies
5V Relay - Water Pump
MOSFET Lamp Circuit
MAX485 RS485 Transceiver
Terminal Blocks Needed: 2 Pin - 2 * 5 = 10 3 Pin - 2 * 5 = 10 4 Pin - 1 * 5 = 5
Heartbeat LED

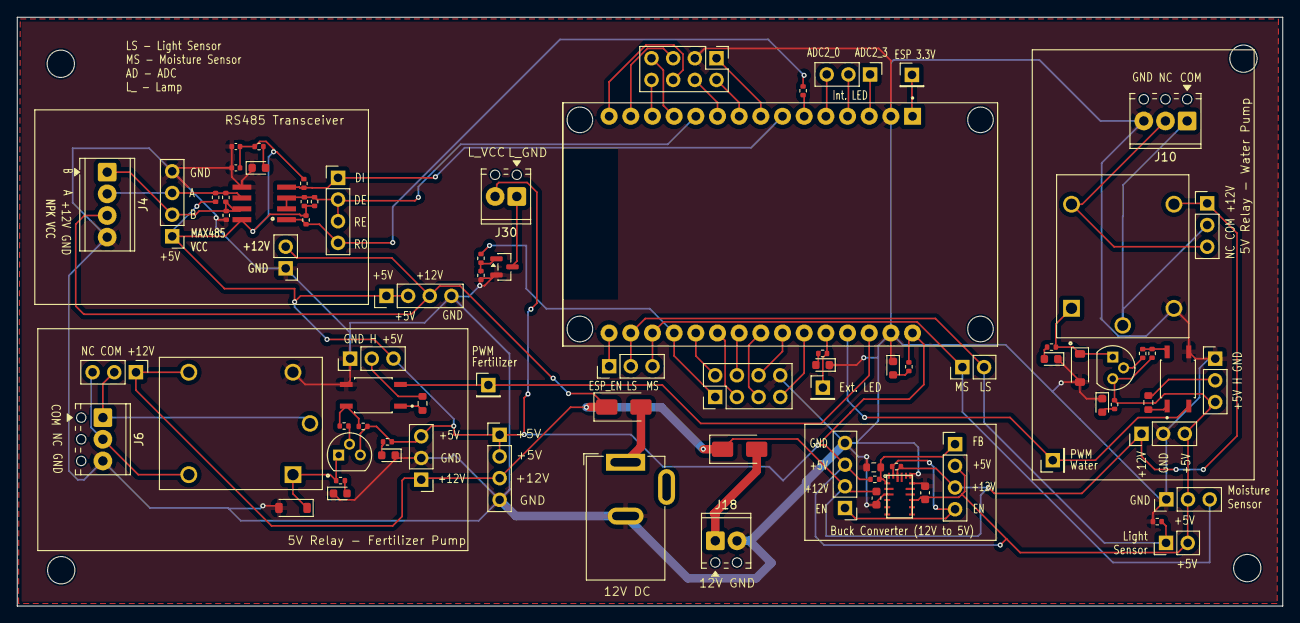
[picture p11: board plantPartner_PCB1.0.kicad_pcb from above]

Board: 2 copper layers, 148.3 x 69.0 mm, 86 parts (0 on the bottom side), 58 nets.

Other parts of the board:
BottomLeft: MountingHole_3.2mm_M3
BottomRight: MountingHole_3.2mm_M3
TopLeft: MountingHole_3.2mm_M3
TopRight: MountingHole_3.2mm_M3

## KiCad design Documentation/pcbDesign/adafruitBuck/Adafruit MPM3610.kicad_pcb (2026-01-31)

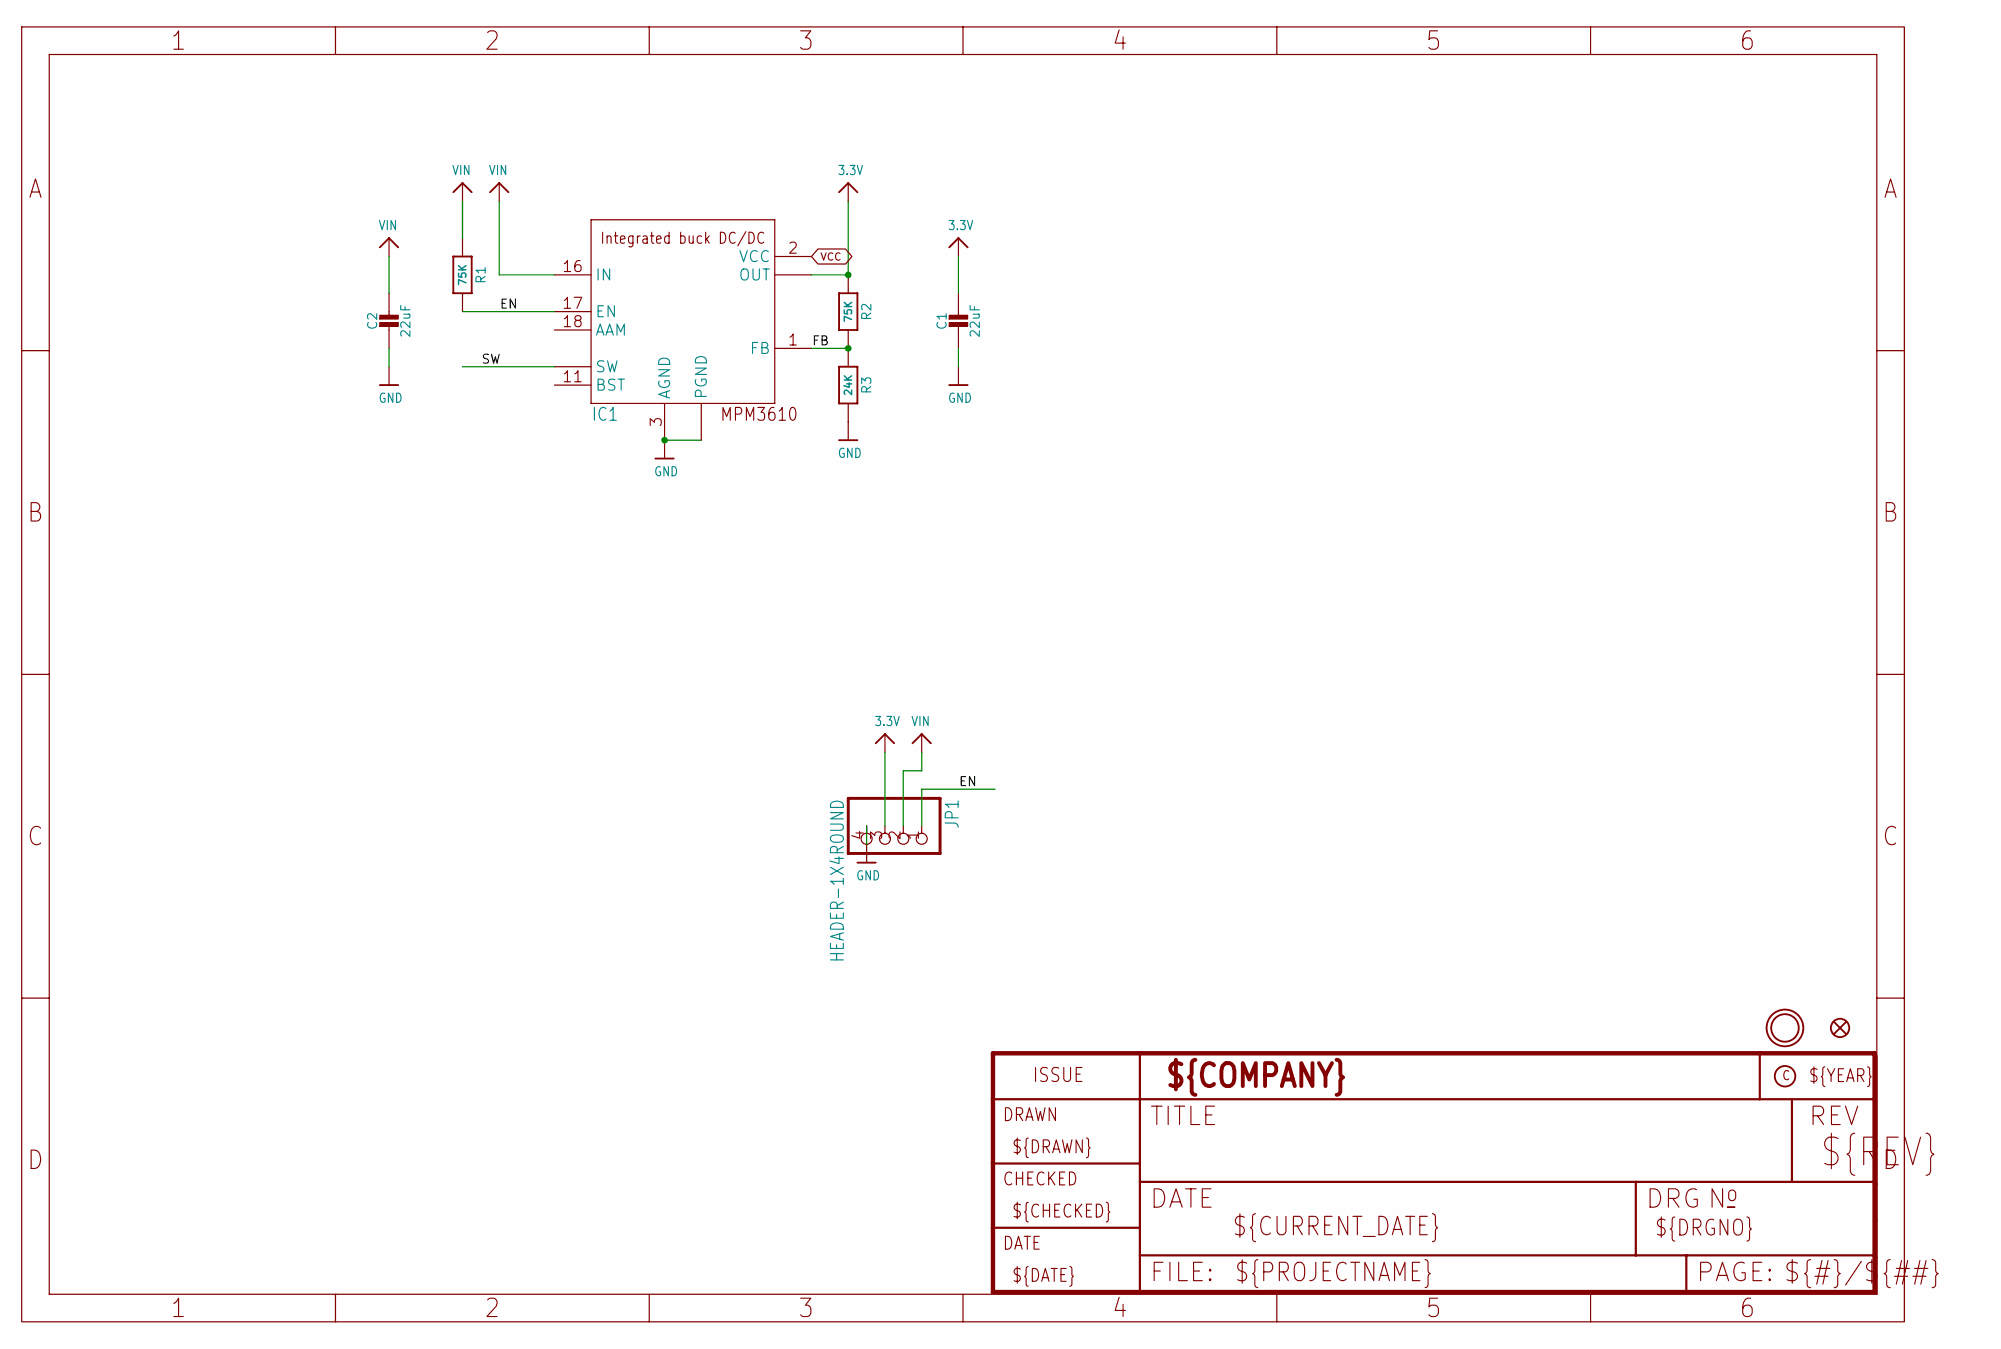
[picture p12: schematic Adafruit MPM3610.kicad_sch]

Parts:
C1, C2: 22uF; 0805-NO
FID1: FIDUCIAL_1MM
IC1: MPM3610
JP1: HEADER-1X4ROUND; 1X04_ROUND
R1, R2: 75K; 0603-NO
R3: 24K; 0603-NO
U$9: MOUNTINGHOLE2.5; MOUNTINGHOLE_2.5_PLATED

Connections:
3.3V: C1.1, IC1.7 (OUT), IC1.8 (OUT), IC1.9 (OUT), JP1.3, R2.1
EN: IC1.17 (EN), JP1.1, R1.2
FB: IC1.1 (FB), R2.2, R3.1
GND: C1.2, C2.2, IC1.3 (AGND), IC1.12 (PGND), IC1.13 (PGND), IC1.14 (PGND), JP1.4, R3.2
SW: IC1.4 (SW), IC1.5 (SW), IC1.6 (SW)
VCC: IC1.2 (VCC)
VIN: C2.1, IC1.16 (IN), JP1.2, R1.1

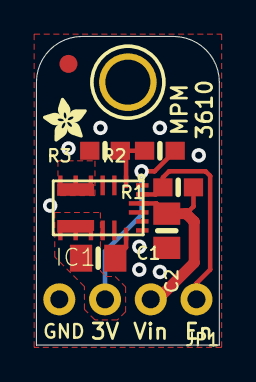
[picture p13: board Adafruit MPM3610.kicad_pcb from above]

Board: 2 copper layers, 10.2 x 17.1 mm, 11 parts (1 on the bottom side), 6 nets.

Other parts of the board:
U$10: PCBFEAT-REV-040
U$11: ADAFRUIT_2.5MM

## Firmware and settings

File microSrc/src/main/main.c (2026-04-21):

// Standard C Libraries
#include <stdio.h>
#include <stdbool.h>
#include <string.h>

// ESP-IDF Libraries
#include "esp_log.h"

// Data Types
#include "../dataTypes/plantData.h"

// Peripherals
#include "../peripherals/adc.h"
#include "../peripherals/gpio.h"
#include "../peripherals/heartbeat.h"
#include "../peripherals/pwm_pump.h"
#include "../peripherals/communication/http.h"
#include "../peripherals/communication/mqtt.h"
#include "../peripherals/communication/wifi.h"
#include "../peripherals/uart_driver.h"
#include "../peripherals/communication/ringbuf.h"

#define MAX_TRANSMISSION_ATTEMPTS            5
const static char *TAG = "DEBUG";

const static char *TOPIC_AUTO_NOTIF = "plant_partner/auto_notif";
const static char *TOPIC_ACT_COMPLETE = "plant_partner/act_compl";
const static char *TOPIC_INIT_TOGGLE = "plant_partner/autocare_startup";
const static char *TOPIC_CHECK_TOGGLE = "plant_partner/act_tog_en";
const static char *TOPIC_CHECK_SENSORS = "plant_partner/ack";
const static char *TOPIC_TASK_MENU    = "plant_partner/task";
const static char *TOPIC_START_UP = "plant_partner/esp_startup";
const static char *ACTIVATION_MESSAGE_AUTOCARE = "Autocare enabled";
const static char *DEACTIVATION_MESSAGE_AUTOCARE = "Autocare disabled";

//Control Messages
const static char *CONTROL_WATER = "water";
const static char *CONTROL_LIGHT = "light";
const static char *CONTROL_NUTRIENTS = "nutrients";
const static char *CONTROL_DEFAULT = "default";

//Handshakes
const static char *MESSAGE_AUTOCARE_ON = "Autocare ON";
const static char *MESSAGE_AUTOCARE_OFF = "Autocare OFF";
const static char *MESSAGE_WATER_DONE = "Water Complete";
const static char *MESSAGE_LIGHT_DONE = "Light Complete";
const static char *MESSAGE_NUTRI_DONE = "Nutrients Complete";

static void water_plant()
{
    modify_pump_duty_cycle(WATER, PWM_DUTY_100_PERCENT);
    vTaskDelay(pdMS_TO_TICKS(700));
    modify_pump_duty_cycle(WATER, 0);
}

static void fertilize_plant()
{
    modify_pump_duty_cycle(FERTLIZER, PWM_DUTY_100_PERCENT);
    vTaskDelay(pdMS_TO_TICKS(700));
    modify_pump_duty_cycle(FERTLIZER, 0);
}

void app_main(void)
{
    // Declare variables
    int adc_raw, voltage;
    bool auto_care_on, light_calibration_successful, moisture_calibration_successful;
    auto_care_on = false;
    const char *message;
    const char *topic;
    esp_err_t err;

    adc_oneshot_unit_handle_t adc1_handle;
    adc_cali_handle_t light_cali_adc1_handle, moisture_cali_adc1_handle;
    light_cali_adc1_handle = moisture_cali_adc1_handle = NULL;

    struct plantData p = {"Sunflower", 1, 2, 3, 4, 5};
    struct plantData *p_ptr = &p;

    // Start up peripheral communication needed to interface with the database
    start_wifi();
    mqtt_app_start();
    esp_http_client_handle_t client;
    client = http_configure_handle();
    http_put_plant_data(client, p_ptr);

    // Initialize ADC for photoresistor and moisture sensor
    light_calibration_successful = adc_init(&adc1_handle, LIGHT, &light_cali_adc1_handle);
    moisture_calibration_successful = adc_init(&adc1_handle, MOISTURE, &moisture_cali_adc1_handle);

    // Configure LEDs
    heartbeat_init();
    configure_IO(OUTPUT, EXTERNAL_LED_GPIO);
    clear_activeHigh_LED(OUTPUT, EXTERNAL_LED_GPIO);

    // Configure PWMs
    pwm_pump_init(WATER);
    pwm_pump_init(FERTLIZER);

    // Initialize UART for RS485 communication with nutrient sensor
    uart_rs485_init();

    publish_mqtt(TOPIC_START_UP, "Start up");

    while (1)
    {
        if (mqtt_check_buffer_ready())
        {
            // Recieve topic and message
            message = read_data();
            topic = read_topic();

            ESP_LOGI("While Loop, Most Recently read ", "Topic: %s, Data: %s", topic, message);

            if (strcmp(topic, TOPIC_INIT_TOGGLE) == 0)
            { 
                if(strcmp(message, "false") == 0)
                    auto_care_on = false;
                else if(strcmp(message, "true") == 0)
                    auto_care_on = true;
                else
                    auto_care_on = !auto_care_on;

                ESP_LOGI(TAG, "Initialized autocare to: %d", auto_care_on);
            }
            // Toggle autocare enable command
            else if (strcmp(topic, TOPIC_CHECK_TOGGLE) == 0)
            {   
                if(strcmp(message, ACTIVATION_MESSAGE_AUTOCARE) == 0)
                {
                    auto_care_on = true;
                    publish_mqtt(TOPIC_AUTO_NOTIF, MESSAGE_AUTOCARE_ON);
                }
                else if(strcmp(message, DEACTIVATION_MESSAGE_AUTOCARE) == 0)
                {
                    auto_care_on = false;
                    publish_mqtt(TOPIC_AUTO_NOTIF, MESSAGE_AUTOCARE_OFF);
                }
                else
                {
                    auto_care_on = !auto_care_on;
                    if(auto_care_on)
                        publish_mqtt(TOPIC_AUTO_NOTIF, MESSAGE_AUTOCARE_ON);
                    else
                        publish_mqtt(TOPIC_AUTO_NOTIF, MESSAGE_AUTOCARE_OFF);
                }

                ESP_LOGI(TAG, "Toggle autocare to: %d", auto_care_on);
            }
            // Read all sensors and send to database
            else if (strcmp(topic, TOPIC_CHECK_SENSORS) == 0)
            {
                // Button functionality for quick actuation
                // If want to just control water
                if(strcmp(message, "water") == 0)
                {
                    water_plant();

                    // Update measured value
                    if (moisture_calibration_successful)
                    {
                        adc_read(MOISTURE, adc1_handle, &adc_raw);
                        adc_rawToVoltage(moisture_cali_adc1_handle, adc_raw, &voltage);

                        if (voltage < 0)
                        {
                            ESP_LOGW(TAG, "Invalid moisture reading", voltage);
                        }
                        else
                        {
                            p_ptr->soilMoisture = voltage;
                        }
                    }

                    ESP_LOGI(TAG, "Water toggled: %d", p_ptr->soilMoisture);

                    // Send data to database
                    http_put_plant_data(client, p_ptr);
                    ESP_LOGI(TAG, "HTTP request...");
                    for (uint8_t try_count = 0; try_count < MAX_TRANSMISSION_ATTEMPTS; try_count++)
                    {
                        err = esp_http_client_perform(client);

                        if (err == ESP_OK)
                            break;
                    }

                    ESP_LOGI(TAG, "HTTP done: %s", esp_err_to_name(err));
                    ESP_LOGI(TAG, "Plant data: Light[%d], Moisture:[%d]", p_ptr->lightIntensity, p_ptr->soilMoisture);

                    // Confirm the actuation was completed
                    publish_mqtt(TOPIC_ACT_COMPLETE, MESSAGE_WATER_DONE);
                }

                // If want to just control light
                else if(strcmp(message, "light") == 0)
                {
                    toggle_activeHigh_LED(OUTPUT, EXTERNAL_LED_GPIO);

                    // Update measured value
                    if (light_calibration_successful)
                    {
                        adc_read(LIGHT, adc1_handle, &adc_raw);
                        adc_rawToVoltage(light_cali_adc1_handle, adc_raw, &voltage);

                        if (voltage < 0)
                        {
                            ESP_LOGW(TAG, "Invalid light reading", voltage);
                        }
                        else
                        {
                            p_ptr->lightIntensity = voltage;
                        }
                    }

                    ESP_LOGI(TAG, "LED toggled: %d", p_ptr->lightIntensity);

                    // Send data to database
                    http_put_plant_data(client, p_ptr);
                    ESP_LOGI(TAG, "HTTP request...");
                    for (uint8_t try_count = 0; try_count < MAX_TRANSMISSION_ATTEMPTS; try_count++)
                    {
                        err = esp_http_client_perform(client);

                        if (err == ESP_OK)
                            break;
                    }
                    ESP_LOGI(TAG, "HTTP done: %s", esp_err_to_name(err));
                    ESP_LOGI(TAG, "Plant data: Light[%d], Moisture:[%d]", p_ptr->lightIntensity, p_ptr->soilMoisture);
                }

                // If want to just control fertilizer
                else if (strcmp(message, "nutrients") == 0)
                {
                    fertilize_plant();

                    // Update measured value
                    ESP_LOGI(TAG, "Reading from RS485-connected nutrient sensor...");
                    uart_rs485_read(p_ptr);
                    ESP_LOGI(TAG, "Finished RS485 read ...");
                    ESP_LOGI(TAG, "Fertilizer toggled: N[%d], P[%d], K[%d]", p_ptr->nLevel, p_ptr->pLevel, p_ptr->kLevel);

                    // Send data to database
                    http_put_plant_data(client, p_ptr);
                    ESP_LOGI(TAG, "HTTP request...");
                    for (uint8_t try_count = 0; try_count < MAX_TRANSMISSION_ATTEMPTS; try_count++)
                    {
                        err = esp_http_client_perform(client);

                        if (err == ESP_OK)
                            break;
                    }

                    ESP_LOGI(TAG, "HTTP done: %s", esp_err_to_name(err));
                    ESP_LOGI(TAG, "Plant data: Light[%d], Moisture:[%d], Nitrogen[%d], Phosphorus:[%d], Potassium:[%d]", 
                             p_ptr->lightIntensity, p_ptr->soilMoisture, p_ptr->nLevel, p_ptr->pLevel, p_ptr->kLevel);

                    // Confirm the actuation was completed
                    publish_mqtt(TOPIC_ACT_COMPLETE, MESSAGE_NUTRI_DONE);
                }
                // If didn't press a button and just want to sample sensors
                else
                {
                    publish_mqtt("plant_partner/state","ENTERED CHECK SENSORS");
                    ESP_LOGI(TAG, "Entered Check Sensors");

                    if (moisture_calibration_successful)
                    {
                        adc_read(MOISTURE, adc1_handle, &adc_raw);
                        adc_rawToVoltage(moisture_cali_adc1_handle, adc_raw, &voltage);

                        if (voltage < 0)
                            ESP_LOGW(TAG, "Invalid moisture reading");
                        else
                            p_ptr->soilMoisture = voltage;
                    }

                    if (light_calibration_successful)
                    {
                        adc_read(LIGHT, adc1_handle, &adc_raw);
                        adc_rawToVoltage(light_cali_adc1_handle, adc_raw, &voltage);

                        if (voltage < 0)
                            ESP_LOGW(TAG, "Invalid light reading");
                        else
                            p_ptr->lightIntensity = voltage;
                    }

                    ESP_LOGI(TAG, "Reading from RS485-connected nutrient sensor...");
                    uart_rs485_read(p_ptr);
                    ESP_LOGI(TAG, "Finished RS485 read...");

                    // Send data to database
                    http_put_plant_data(client, p_ptr);
                    ESP_LOGI(TAG, "HTTP request...");
                    for (uint8_t try_count = 0; try_count < MAX_TRANSMISSION_ATTEMPTS; try_count++)
                    {
                        err = esp_http_client_perform(client);
                        if (err == ESP_OK)
                            break;
                    }
                    ESP_LOGI(TAG, "HTTP done: %s", esp_err_to_name(err));
                    ESP_LOGI(TAG, "Plant data: Light[%d], Moisture:[%d], N[%d], P[%d], K[%d]",
                            p_ptr->lightIntensity, p_ptr->soilMoisture,
                            p_ptr->nLevel, p_ptr->pLevel, p_ptr->kLevel);
                }
            }
            // Task menu
            else if (strcmp(topic, TOPIC_TASK_MENU) == 0)
            {
                ESP_LOGI(TAG, "ENTER TASK MENU WITH MESSAGE: %s", message);
                if(strstr(message, CONTROL_WATER) != NULL)
                {
                    publish_mqtt("plant_partner/state","ENTERED Water");

                    if(auto_care_on)
                    {
                        // Check moisture before watering
                        if (moisture_calibration_successful)
                        {
                            adc_read(MOISTURE, adc1_handle, &adc_raw);
                            adc_rawToVoltage(moisture_cali_adc1_handle, adc_raw, &voltage);

                            if (voltage < 0)
                                ESP_LOGW(TAG, "Invalid moisture reading");
                            else
                                p_ptr->soilMoisture = voltage;
                        }

                        if (p_ptr->soilMoisture < MOISTURE_THRESHOLD)
                            ESP_LOGI(TAG, "WET: ADC%d Channel[%d] Showing How Wet: %d ", ADC_UNIT_1 + 1, ADC_MOISTURE_CHANNEL, p_ptr->soilMoisture);
                        else
                        {
                            ESP_LOGI(TAG, "DRY: ADC%d Channel[%d] Showing How Wet: %d ", ADC_UNIT_1 + 1, ADC_MOISTURE_CHANNEL, p_ptr->soilMoisture);
                            water_plant();
                        }
                    }
                    else
                    {
                        water_plant();

                        if (moisture_calibration_successful)
                        {
                            adc_read(MOISTURE, adc1_handle, &adc_raw);
                            adc_rawToVoltage(moisture_cali_adc1_handle, adc_raw, &voltage);

                            if (voltage < 0)
                                ESP_LOGW(TAG, "Invalid moisture reading");
                            else
                                p_ptr->soilMoisture = voltage;
                        }
                        ESP_LOGI(TAG, "Water toggled: %d", p_ptr->soilMoisture);
                    }

                    publish_mqtt(TOPIC_ACT_COMPLETE, MESSAGE_WATER_DONE);
                }
                if(strstr(message, CONTROL_LIGHT) != NULL)
                {
                    publish_mqtt("plant_partner/state","ENTERED Light");
                    if(auto_care_on)
                    {
                        // Check light before enabling
                        if (light_calibration_successful)
                        {
                            adc_read(LIGHT, adc1_handle, &adc_raw);
                            adc_rawToVoltage(light_cali_adc1_handle, adc_raw, &voltage);

                            if (voltage < 0)
                                ESP_LOGW(TAG, "Invalid light reading");
                            else
                                p_ptr->lightIntensity = voltage;
                        }

                        if (p_ptr->lightIntensity < LED_THRESHOLD)
                        {
                            set_activeHigh_LED(OUTPUT, EXTERNAL_LED_GPIO);
                            ESP_LOGI(TAG, "LED ON: Light %d mV is below threshold", p_ptr->lightIntensity);
                        }
                        else
                        {
                            clear_activeHigh_LED(OUTPUT, EXTERNAL_LED_GPIO);
                            ESP_LOGI(TAG, "LED OFF: Light %d mV is above threshold", p_ptr->lightIntensity);
                        }
                        
                    }
                    else
                    {
                        toggle_activeHigh_LED(OUTPUT, EXTERNAL_LED_GPIO);

                        if (light_calibration_successful)
                        {
                            adc_read(LIGHT, adc1_handle, &adc_raw);
                            adc_rawToVoltage(light_cali_adc1_handle, adc_raw, &voltage);

                            if (voltage < 0)
                                ESP_LOGW(TAG, "Invalid light reading");
                            else
                                p_ptr->lightIntensity = voltage;
                        }
                        ESP_LOGI(TAG, "LED toggled: %d", p_ptr->lightIntensity);
                    }

                    publish_mqtt(TOPIC_ACT_COMPLETE, MESSAGE_LIGHT_DONE);
                }
                if(strstr(message, CONTROL_NUTRIENTS) != NULL)
                {
                    publish_mqtt("plant_partner/state","ENTERED Nutrients");
                    if(auto_care_on)
                    {
                        // Check NPK before fertilizing
                        ESP_LOGI(TAG, "Reading from RS485-connected nutrient sensor...");
                        uart_rs485_read(p_ptr);
                        ESP_LOGI(TAG, "Finished RS485 read ...");

                        if (p_ptr->nLevel + p_ptr->pLevel + p_ptr->kLevel < NPK_THRESHOLD)
                        {
                            ESP_LOGI(TAG, "LOW NUTRIENTS: Current sum[%d] is below threshold", p_ptr->nLevel + p_ptr->pLevel + p_ptr->kLevel);

                            fertilize_plant();
                        }
                        else
                        {
                            ESP_LOGI(TAG, "GOOD NUTRIENTS: Current sum[%d] is above threshold", p_ptr->nLevel + p_ptr->pLevel + p_ptr->kLevel);
                        }
                    }
                    else
                    {
                        fertilize_plant();

                        ESP_LOGI(TAG, "Reading from RS485-connected nutrient sensor...");
                        uart_rs485_read(p_ptr);
                        ESP_LOGI(TAG, "Finished RS485 read ...");
                        ESP_LOGI(TAG, "Fertilizer toggled: N[%d], P[%d], K[%d]",
                                 p_ptr->nLevel, p_ptr->pLevel, p_ptr->kLevel);
                    }

                    publish_mqtt(TOPIC_ACT_COMPLETE, MESSAGE_NUTRI_DONE);
                }
                
                // Send data to database
                http_put_plant_data(client, p_ptr);
                ESP_LOGI(TAG, "HTTP request...");
                for (uint8_t try_count = 0; try_count < MAX_TRANSMISSION_ATTEMPTS; try_count++)
                {
                    err = esp_http_client_perform(client);
                    if (err == ESP_OK)
                        break;
                }
                ESP_LOGI(TAG, "HTTP done: %s", esp_err_to_name(err));
            }
            else
            {
                ESP_LOGI(TAG, "ERROR, TOPIC: %s IS NOT RECOGNIZED", topic);
            }
        }

    vTaskDelay(pdMS_TO_TICKS(200));
    }
}

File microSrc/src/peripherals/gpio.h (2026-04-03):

#ifndef GPIO_LED_H
#define GPIO_LED_H

#include "driver/gpio.h"

#define LED_THRESHOLD          1000  // Voltage threshold in mV for LED control
#define EXTERNAL_LED_GPIO      GPIO_NUM_23
#define INTERNAL_BLUE_LED_GPIO GPIO_NUM_2
#define SWITCH0_GPIO           GPIO_NUM_35
#define SWITCH1_GPIO           GPIO_NUM_32
#define SWITCH2_GPIO           GPIO_NUM_33
#define SWITCH3_GPIO           GPIO_NUM_25
#define SWITCH4_GPIO           GPIO_NUM_26
#define OUTPUT                 true
#define INPUT                  false

// GPIO Configuration & Control for active High LEDs
void configure_IO(bool ioType, uint8_t gpio_num);
void initialize_interrupts();
void set_activeHigh_LED(bool ioType, uint8_t gpio_num);
void clear_activeHigh_LED(bool ioType, uint8_t gpio_num);
void toggle_activeHigh_LED(bool ioType, uint8_t gpio_num);

#endif // GPIO_LED_H

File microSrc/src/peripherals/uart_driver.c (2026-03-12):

#include "uart_driver.h"
#include <string.h>

static const char *UART_TAG = "uart_driver";

void uart_init(const uart_port_t uartPort)
{
    // Install UART Driver
    ESP_ERROR_CHECK(uart_driver_install(uartPort, UART_RX_BUFFER_SIZE, UART_TX_BUFFER_SIZE, 0, NULL, 0));

    // Setup UART Port Configuration
    uart_config_t uart_config = {
        .baud_rate = UART_BAUD_RATE,
        .data_bits = UART_DATA_8_BITS,
        .parity    = UART_PARITY_DISABLE,
        .stop_bits = UART_STOP_BITS_1,
        .flow_ctrl = UART_HW_FLOWCTRL_DISABLE,
    };
    ESP_ERROR_CHECK(uart_param_config(uartPort, &uart_config));

    // Set ESP pins for respective UART Port
    switch (uartPort)
    {
        case UART_PORT0:
            ESP_ERROR_CHECK(uart_set_pin(uartPort, UART0_TX_PIN, UART0_RX_PIN, UART_PIN_NO_CHANGE, UART_PIN_NO_CHANGE));
            break;
        case UART_PORT1:
            ESP_ERROR_CHECK(uart_set_pin(uartPort, UART1_TX_PIN, UART1_RX_PIN, UART1_RTS_PIN, UART1_CTS_PIN));
            break;
        case UART_PORT2:
            ESP_ERROR_CHECK(uart_set_pin(uartPort, UART2_TX_PIN, UART2_RX_PIN, UART2_RTS_PIN, UART2_CTS_PIN));
            break;
        default:
            ESP_ERROR_CHECK(uart_set_pin(uartPort, UART0_TX_PIN, UART0_RX_PIN, UART_PIN_NO_CHANGE, UART_PIN_NO_CHANGE));
            break;
    }
}

void uart_kill(const uart_port_t uartPort)
{
    // Delete UART driver if already installed
    if (uart_is_driver_installed(uartPort)) 
    {
        ESP_ERROR_CHECK(uart_driver_delete(uartPort));
    }
}

uart_error_t uart_write_bytes_blocking(const uart_port_t uartPort, const void *data, size_t numBytes)
{
    // Check if requested driver is initialized
    if (!uart_is_driver_installed(uartPort)) 
    {
        ESP_LOGE(UART_TAG, "write: driver not installed for port %d", uartPort);
        return UART_ERROR_DRIVER_NOT_INSTALLED;
    }

    // Send data - Check if data pointer is NULL, if numBytes is 0, or if nothing written
    if (data == NULL) 
    {
        ESP_LOGE(UART_TAG, "write: data pointer is NULL");
        return UART_ERROR_WRITE_FAILED;
    }

    if (numBytes == 0) 
    {
        numBytes = strlen((const char *)data);
    }

    int written = uart_write_bytes(uartPort, (const char *)data, numBytes);
    if (written < 0) 
    {
        return UART_ERROR_WRITE_FAILED;
    }

    // Wait a set 100 ticks for transmission to complete
    ESP_ERROR_CHECK(uart_wait_tx_done(uartPort, UART_TICKS_TO_WAIT));
    return UART_ERROR_NONE;
}

uart_error_t uart_write_string(const uart_port_t uartPort, const char *s)
{
    // Check if string is empty then write
    if (s == NULL)
    {
        return UART_ERROR_WRITE_FAILED;
    }

    return uart_write_bytes_blocking(uartPort, s, strlen(s));
}

uart_error_t uart_write_int(const uart_port_t uartPort, int v)
{
    // Convert integer to ASCII string and send
    char buf[32];
    int n = snprintf(buf, sizeof(buf), "%d\n", v);

    if (n < 0)
    {
        return UART_ERROR_WRITE_FAILED;
    } 

    return uart_write_bytes_blocking(uartPort, buf, (size_t)n);
}

uart_error_t uart_read_bytes_blocking(const uart_port_t uartPort, void *buf)
{
    // Check if requested driver is initialized
    if (!uart_is_driver_installed(uartPort)) 
    {
        ESP_LOGE(UART_TAG, "read: driver not installed for port %d", uartPort);
        return UART_ERROR_DRIVER_NOT_INSTALLED;
    }

    // Read in Receive FIFO
    int readBufferLength; 
    ESP_ERROR_CHECK(uart_get_buffered_data_len(uartPort, (size_t*)&readBufferLength));

    // Check if readBufferLength is longer than 256 bytes and clamp if needed
    if (readBufferLength > UART_RX_MAX_LENGTH)
    {
        readBufferLength = 255;
    }

    if (readBufferLength <= 0)
    {
        return UART_ERROR_NO_BYTES_TO_READ;
    }

    // Read in Bytes to buffer
    uart_read_bytes(uartPort, buf, readBufferLength, UART_TICKS_TO_WAIT);
    return UART_ERROR_NONE;
}

// --------------------------------------------------------------------------- //
// Code meant for our specific rs485 communication for the NPK sensor          //
// --------------------------------------------------------------------------- //
// Compute Modbus CRC16 (polynomial 0xA001), returns 16-bit CRC (LSB first when sent)
static uint16_t modbus_crc16(const uint8_t *buf, int len)
{
    uint16_t crc = 0xFFFF;
    for (int pos = 0; pos < len; pos++) 
    {
        crc ^= (uint16_t)buf[pos];
        for (int i = 0; i < 8; i++) 
        {
            crc = (crc & 0x0001) ? ((crc >> 1) ^ 0xA001) : (crc >> 1);
        }
    }
    return crc;
}
void uart_rs485_init()
{
    // RS485 uses UART2 //
    // Install UART Driver: Only Receiving Buffer
    ESP_ERROR_CHECK(uart_driver_install(UART_PORT2, UART_RX_BUFFER_SIZE, UART_TX_BUFFER_SIZE, 0, NULL, 0));
    ESP_LOGI(UART_TAG, "UART2 driver installed with RX buffer size %d and TX buffer size %d", UART_RX_BUFFER_SIZE, UART_TX_BUFFER_SIZE);

    // UART Port Configuration for RS485
    uart_config_t uart_config = {
        .baud_rate = UART_RS485_BAUD_RATE,
        .data_bits = UART_DATA_8_BITS,
        .parity    = UART_PARITY_DISABLE,
        .stop_bits = UART_STOP_BITS_1,
        .flow_ctrl = UART_HW_FLOWCTRL_DISABLE,
    };
    ESP_ERROR_CHECK(uart_param_config(UART_PORT2, &uart_config));
    ESP_LOGI(UART_TAG, "UART2 configured for RS485 communication at %d baud, %d data bits, %d stop bits, and %d parity", UART_RS485_BAUD_RATE, uart_config.data_bits, uart_config.stop_bits, uart_config.parity);

    // Set ESP Pins for UART2 (RS485)
    ESP_ERROR_CHECK(uart_set_pin(UART_PORT2, UART2_TX_PIN, UART2_RX_PIN, UART_PIN_NO_CHANGE, UART_PIN_NO_CHANGE));
    ESP_LOGI(UART_TAG, "UART2 pins set: TX=%d, RX=%d, RTS=%d, CTS=%d, DE/RE=%d", UART2_TX_PIN, UART2_RX_PIN, UART_PIN_NO_CHANGE, UART_PIN_NO_CHANGE, RS485_DE_RE_PIN);

    // Initialize DE/RE Pin Control to Receive Mode (Low) - Transmit Mode is High
    gpio_reset_pin(RS485_DE_RE_PIN);
    gpio_set_direction(RS485_DE_RE_PIN, GPIO_MODE_OUTPUT);
    gpio_set_level(RS485_DE_RE_PIN, 0);
}
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

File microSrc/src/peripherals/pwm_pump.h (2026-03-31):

#ifndef PWM_PUMP_H
#define PWM_PUMP_H

#include "driver/gpio.h"
#include "driver/ledc.h"

#define PWM_WATER_MOTOR_PIN         GPIO_NUM_4
#define PWM_FERTILIZER_MOTOR_PIN    GPIO_NUM_15
#define PWM_TIMER                   LEDC_TIMER_0
#define PWM_MODE                    LEDC_LOW_SPEED_MODE
#define PWM_WATER_CHANNEL           LEDC_CHANNEL_0
#define PWM_FERTILIZER_CHANNEL      LEDC_CHANNEL_1
#define PWM_RESOLUTION              LEDC_TIMER_8_BIT
#define PWM_FREQUENCY_HZ            4000
#define PWM_DUTY_100_PERCENT        255
#define PWM_DUTY_50_PERCENT         128
#define PWM_DUTY_0_PERCENT          0
#define FERTLIZER                   true
#define WATER                       false


// PWM Initialization and Configuration Functions
void pwm_pump_init(bool component);
void modify_pump_duty_cycle(bool component, uint8_t duty_cycle);

#endif // PWM_PUMP_H

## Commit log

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2025-10-20 remade timesheet, broke
    [TimeReport_SabrinaLuu.xlsx]
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2025-10-25 Made just one init that does error handling
    [main.c]
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2025-10-25 Update README with completed work and current bugs
    Added completed work section and current bugs information.
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2025-10-26 Fixing timesheet conflicts
    [TimeReport_SabrinaLuu.xlsx]
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2025-10-26 Fixing merge conflict temporarily
    [TimeReport_NicholasCimino.xlsx]
2025-10-26 Nicholas - Attempting to fix Timesheet in Main Branch
    [TimeReport_NicholasCimino.xlsx]
2025-11-04 Added PCB Design files into new pcbDesign Directory. Got ESP-IDF working on my Windows and figured out ESP-32 Model (I think 99% sure). Updated timesheets also
    [TimeReport_CarterKreis.xlsx, plantPartner_PCB1.0.kicad_pcb, plantPartner_PCB1.0.kicad_sch]
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2025-11-06 Nicholas - Updated Hours. Also updated backEndSrc to set up an HTTP server for HTTP requests and communications from other devices
    [TimeReport_NicholasCimino.xlsx]
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2025-11-10 Missed a name change
    [adc.h]
2025-11-10 Adjust end time due to making fix
    [TimeReport_AspenBoler.xlsx]
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2025-11-11 Base format for post functionality, can fetch plant data from backend, update timesheet
    [TimeReport_SabrinaLuu.xlsx]
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2025-11-13 Updated start/end time, able to display data from backend onto homescreen, currently unformatted
    [TimeReport_SabrinaLuu.xlsx]
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2025-11-13 Accidentally broke build in merge, but it's fixed now I swear
    [TimeReport_AspenBoler.xlsx]
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2026-01-06 Implemented 5V Relay to our specs. Time to verify it and add AC to 12V Adapter to overall schematic then draw PCB
    [plantPartner_PCB1.0.kicad_sch]
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2026-01-08 ADC reworked and confirmed to function correctly
    [adc.c, adc.h, main.c]
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2026-01-17 Provided set up for switch and LED that'll increase predictability of behavior
    [TimeReport_AspenBoler.xlsx]
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2026-01-23 Verified the Schematic designs for the RS-485 Transceiver and Buck Converter. I will verify the 5V Relay next and then start routing the PCB itself ASAP
    [plantPartner_PCB1.0.kicad_pcb, plantPartner_PCB1.0.kicad_sch]
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2026-01-24 Since I was able to copy the Buck Converter and RS-485 Relay verbatim from an online source, verifying them was rather quick but for this 5V relay I am trying to properly simulate and probe its volta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
    [plantPartner.kicad_sch, plantPartner_PCB1.0.kicad_pcb, plantPartner_PCB1.0.kicad_sch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]
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2026-01-26 Verified circuit. Time to finalize Schematic with symbols that have compatible footprints. Need to add remaining 3D models, testing pins for PCB, and verify relay octocoupler footprint + symbol
    [Adafruit MPM3610.kicad_pcb, Adafruit MPM3610.kicad_sch, buckConverter.kicad_pcb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]
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2026-01-28 Put in the correct ESP32 (DEVKIT-V1) into Schematic. Updated the IO pin connections for ESP. Added Power supply system to SChematic. Need to update optocoupler symbol and footprint. Then routing shal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
    [TimeReport_AspenBoler.xlsx, TimeReport_SabrinaLuu.xlsx, plantPartner_PCB1.0.kicad_sch]
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2026-01-29 Added the small circuitry needed for ADC sensors, ESP-32 External LED, Overall PCB Heartbeat sensor. Fixed wiring issue with 5V Relays. Met with Prof. Alex about our Alpha Build status. I tried to ad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
    [plantPartner_PCB1.0.kicad_pcb, plantPartner_PCB1.0.kicad_sch]
2026-01-31 Fixed optocoupler for Relay circuits
    [plantPartner_PCB1.0.kicad_pcb, plantPartner_PCB1.0.kicad_sch]
2026-01-31 Added Labels to majority of unused ESP32 Pins. I will fill in the rest later
    [plantPartner_PCB1.0.kicad_sch]
2026-02-05 Finished adding Testing Pins. Starting Routing by drawing it out and organizing components in PCB. Quickly realized that I incorrectly setup 5V and 12V labels so will need to re-label those soon
    [TimeReport_CarterKreis.xlsx, plantPartner_PCB1.0.kicad_pcb, plantPartner_PCB1.0.kicad_sch]
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2026-02-06 We showed off the Alpha Build to Tyler and I worked on the PCB Routing. I am trying to resolve the Electrical Rules Checker (ERC) now while routing.
    [TimeReport_CarterKreis.xlsx, plantPartner_PCB1.0.kicad_pcb, plantPartner_PCB1.0.kicad_sch]
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2026-02-08 Routed the 5V Relays and fixed a schematic issue I made with them. Next is the Buck Converter, RS485 Transceiver, Power Supplies, and ESP32 Signals
    [plantPartner_PCB1.0.kicad_pcb, plantPartner_PCB1.0.kicad_sch]
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2026-02-10 Fixed Buck Converter and routed it. Connected more majority of ESP signals and some of the debugging pins. Brought the size of PCB down to about 1/2 of the original. My goal is to finish by today and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
    [Adafruit MPM3610.kicad_pcb, plantPartner_PCB1.0.kicad_pcb, plantPartner_PCB1.0.kicad_sch]
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2026-02-12 Finished Routing (for now). I need to add silkscreens for debugging, then copper pour and probably other stuff. My goal is so have a JLCPCB order by tomorrow. I brought the PCB down to about the size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
    [plantPartner_PCB1.0.kicad_pcb, plantPartner_PCB1.0.kicad_sch]
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2026-02-12 Reversing direct comm changes
    [main.c]
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2026-02-13 Finished Labeling PCB (too much) and fixed DRC errors on PCB. Time to add copper pours, drill holes, and probably more, then review it with a TA, and make the order :)
    [plantPartner_PCB1.0.kicad_pcb, plantPartner_PCB1.0.kicad_sch]
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2026-02-13 Meeting with Tyler. I tried to implement Lamp Circuit with MOSFET but having trouble simulating it in LTspice
    [TimeReport_CarterKreis.xlsx, plantPartner_PCB1.0.kicad_pcb, plantPartner_PCB1.0.kicad_sch]
2026-02-14 Finally got LTspice sim to work and confirmed that Schematic is good. Time to implement into PCB
    [TimeReport_CarterKreis.xlsx]
2026-02-15 Added Lamp to PCB. Added Copper Pours and Drill Holes. Now fixing rude error about cap. not getting copper pour connection properly
    [plantPartner_PCB1.0.kicad_pcb, plantPartner_PCB1.0.kicad_sch]
2026-02-16 Gerber and Drill files have been generated. I will order on JLCPCB tomorrow morning ASAP and then finish up cube for Beta
    [plantPartner_PCB1.0-B_Cu.gbl, plantPartner_PCB1.0-B_Mask.gbs, plantPartner_PCB1.0-B_Silkscreen.gbo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]
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2026-02-19 Made some adjustments to PCB to fit JLCPCB standards. When going to order PCB realized I needed LCSC values. I spent the rest of the time trying to setup the JLCPCB tools plugin with zero success.
    [plantPartner_PCB1.0-B_Cu.gbl, plantPartner_PCB1.0-B_Mask.gbs, plantPartner_PCB1.0-B_Paste.gbp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]
2026-02-19 I got the plugin finally working! I had some messed up Python modules that I had to remove and then reinstall. I have also now learned that the footprints I chose for the PCB were too small and class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
    [BOM-plantPartner_PCB1.0.csv, TimeReport_CarterKreis.xlsx, mapping.csv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]
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2026-02-19 Rerouted the resistors, capacitors, and LEDs. Surely I can now generate the Drill & Gerber files for printing with no issues
    [TimeReport_CarterKreis.xlsx, plantPartner_PCB1.0.kicad_pcb, plantPartner_PCB1.0.kicad_sch]
2026-02-20 Started JLCPCB order process. Need to evaluate cheapest options, out-of-stock replacements, and parts JLCPCB does not have at all
    [BOM-plantPartner_PCB1.0.csv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]
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2026-02-20 I ordered the PCBgit add . … there is so many changes I want to make but I also just wanted to order it but without the revisions it was more expensive but now we at least will have a board. Welp, ei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
    [BOM-plantPartner_PCB1.0.csv, TimeReport_CarterKreis.xlsx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]
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2026-02-24 Added basic implementation of 2.0 changes to see how much cheaper new PCB would be. As of now, it is half the price :O
    [BOM-plantPartner_PCB2.0.csv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]
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2026-02-27 I still need to test MOSFET circuits in Ltspice but I cleaned up the v2 Schematic and starting routing v2 PCB
    [TimeReport_CarterKreis.xlsx, plantPartner_PCB2.0.kicad_pcb, plantPartner_PCB2.0.kicad_sch]
2026-02-27 I think current reference is outdated, trying to fix
2026-03-01 Routed v2 PCB some more. Finished routing power sources, Buck Converter, MOSFET circuits, and most of RS485 Transceiver. I forgot about KiCad but will not next time I get a big chunk of time
    [TimeReport_CarterKreis.xlsx, plantPartner_PCB2.0.kicad_pcb, plantPartner_PCB2.0.kicad_sch]
2026-03-02 Meeting with Tyler. Fully finished routing MOSFET circuits, RS485 Transceiver, and some of ADC circuits. Still need to test MOSFET circuits in Ltspice, but placed most of overall PCB into a small edg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
    [TimeReport_CarterKreis.xlsx, plantPartner_PCB2.0.kicad_pcb, plantPartner_PCB2.0.kicad_sch]
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2026-03-02 Finished routing everything. Adding silkscreens and double checking details. Next I will test in Ltspice. Hopefully, place JLC order by tonight or tomorrow
    [TimeReport_CarterKreis.xlsx, plantPartner_PCB2.0.kicad_pcb, plantPartner_PCB2.0.kicad_sch]
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2026-03-04 I made an oopsie with PCBv2 order so I had to fix that and in the meantime I found a cheaper solution that kept the same logic of the circuits. It saved us 0 yippee
    [BOM-plantPartner_PCB2.0.csv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]
2026-03-04 I got it working! I adjusted the CRC checker and added a delay when switching between Receive and Transmit mode. The data looks valid and increases or decreases when in or out of dirt. Next I'll clea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
    [main.c, uart_driver.c, uart_driver.h]
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2026-03-24 Updating Timesheet ... yeah I got no idea why I didn't merge my latest timesheet into main lol
    [TimeReport_CarterKreis.xlsx]
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2026-03-31 Merged main in and nothing broke with new pin assignments (it compiled)
2026-03-31 Revert IP and fix led pin, ALSO PCB WORKS
    [gpio.h]
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2026-04-02 Nicholas - switched URI's for mqtt to use test mosquittto broker again
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
